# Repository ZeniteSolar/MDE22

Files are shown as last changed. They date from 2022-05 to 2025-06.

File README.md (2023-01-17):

# Electric Steering for Solar Boat

Instituto Federal de Educação, Ciência e Tecnologia de Santa Catarina - Campus Florianópolis

Electronics Academic Department

Degree in Electronics Engineering

Course: Integrative Project III

Professors:

* Robinson Pizzio and Daniel Lohmann

Student:

* Gabriel Ayres Rodrigues

# Summary

1. [Introduction](#introduction)
2. [Conception](#conception)
3. [Design](#design)
4. [Implementation](#implementation)
5. [Operation](#operation)
6. [Considerations](#considerations)
7. [References](#references)

# Introduction

This module aims to control the direction of the tail of the Guarapuvu II vessel, belonging to the IFSC Zênite Solar team.

It is inspired by the previously implemented system, developed by Cesar Dias Parente. The project files can be found [here](https://github.com/ZeniteSolar/MDE18/tree/main).

The Zênite team vessel is operated in solar boat competitions, where high performance and robustness are required. Being the only boat to use electric steering on the competition's context, the team counts on a more reliable system and is able to outmaneuver competition, which is a significant advantage on the Slalom race

The current electronic system was damaged after the competition in March 2022, which is a motivator for its upgrade.

# Conception

Thinking about a steering system, choosing to use an electric steering can bring greater responsiveness even though it has a fraction of the weight of a mechanical system. In addition, mechanical systems can require physical effort from the driver and a greater need for maintenance. 

Below is the diagram representing an electric steering system and its parts.
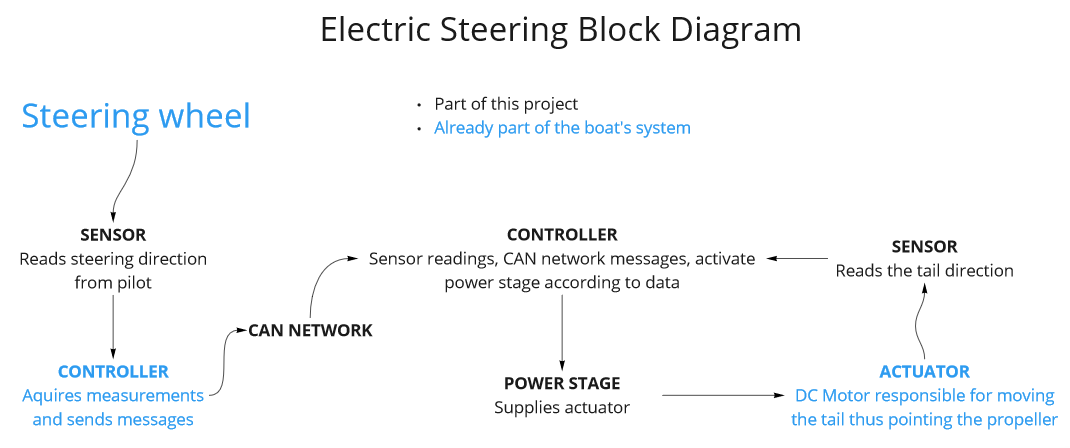
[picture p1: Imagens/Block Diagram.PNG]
Diagram


Taking into account the above elements, the following problems must be confronted:
- Electronic systems in vehicles must have high robustness due to the vibrations to which they are exposed. In the case of high speed vessels, especially for marine operations, impacts are a big problem (besides oxidation of the circuits).
- As the target vehicle is used in competitions whose focus, and therefore the challenge, is on energy generation and consumption, the solution must be as efficient as possible to ensure the success of the team.
- A competitive environment between vehicles requires high performance from this equipment, not only to achieve victory but to ensure everyone's safety. Therefore, the functionality must be met as well as the other parameters.

To implement the whole, it is necessary to define the requirements of the parts, and the possible proposals to satisfy them.

* ## Sensors

There are some options for rotation sensors such as: inductive, optical, Hall effect sensor, rotation potentiometer, encoder. The most economical and simple-to-implement alternative is a common linear potentiometer, currently used in the Zênite team system.

The most used types for steering sensors on the market are the following: resistive, encoders, and those with GMR technology ([Giant magnetoresistance](https://en.wikipedia.org/wiki/Giant_magnetoresistance)). (see the companies considered in [References](#references))

Sensors of this level are state-of-the-art and therefore out of the question, however it is worth noting that the resistive sensor is still being used (even in common vehicles, such as the [butterfly position sensor](https://www.dpk.com.br/como-funciona-o-sensor-de-posicao-da-borboleta/)).

For a contrast between the leaders: resistive sensors have a disadvantage due to wear and possible poor contact, GMR can suffer interference in environments with a strong magnetic field, and encoders (because they are digital) present a challenge in the trade-off Precision X Complexity (thus, price).

Seeking the balance between robustness, ease of implementation and price, the resistive sensor stands out.
 
* ## Controller

The implemented CAN network eliminates the need for cabling with analog signal between the stern and the bow. This ensures noise reduction in sensor readings and takes advantage of existing CAN cabling, compacting the system.

In addition, communication over the network makes it possible for the module to send data and control the direction using messages from other modules. In this way, the range is open for future implementations that may include:

	Redundancy messages and/or sensors
	Low Power Mode - Enabled by the Data Processing Module
	remote steering

A commercial line microcontroller will be enough to guarantee the execution of the desired tasks and response time. In addition to PWM ports and ADC inputs, a microcontroller with a CAN interface like the STM32F103xx or equivalent would be interesting. However, this alternative exceeds the price of IC's transceiver and CAN interface, in addition its programming is more laborious.

Due to its ease of programming and price, the [ATmega328P](https://br.mouser.com/ProductDetail/Microchip-Technology-Atmel/ATMEGA328P-PU?qs=K8BHR703ZXguOQv3sKbWcg%3D%3D) is proposed. For the connection to the CAN network, the most common and affordable IC's are the transceiver
[MCP2551](https://br.mouser.com/datasheet/2/268/20001667G-1115479.pdf) and the CAN/SPI interface circuit [MCP2515](https://br.mouser.com/datasheet/ 2/268/MCP2515_Family_Data_Sheet_DS20001801K-2303489.pdf).

The steering wheel potentiometer reading function will be performed by another module already present in the bow: [MIC19](https://github.com/ZeniteSolar/MIC19)

* ## Power Circuit

The brushed DC motor is driven by an H bridge, currently powered by a 12V battery. The current circuit is implemented by two half-bridge integrated [BTS7960](https://pdf1.alldatasheet.com/datasheet-pdf/view/152657/INFINEON/BTS7960.html).

This component was discontinued, and the best alternative found was [FAN7093](https://www.mouser.com/datasheet/2/149/FAN7093-76982.pdf). As the current one is already in hand and this project is focused on integration and telemetry, the same integrated circuit was used.

* ## Measurements and Feedback

It is essential to provide the CAN network with data on power consumption, as it is a battery-powered power system. Therefore, a current sensor is proposed for each arm of the H-bridge.

Conveniently, the BTS7960 half-bridge integrated circuit has an output pin for current sensing — a current source is connected to the output, and the current IS is proportional to the load current IL according to the measuring resistor RIS.

Alternatively, a circuit like the [INA240](https://www.ti.com/lit/ds/symlink/ina240.pdf?ts=1649772128538) ultra-precise bidirectional current sensor with PWM rejection could be used. From the same family of IC's, the INA826 will be used to measure battery voltage (Hbridge voltage).

These measurements should contribute to the feedback, which will also have the tail position data. Bringing this data to a display ensures that the pilot is aware of the state of the system and the consumption that his riding is causing.

# Design

The module was developed with Kicad software, the project is in the hardware folder of this git and its complete schematic can be viewed [here](https://github.com/ayresgit/Modulo-Direcao-Eletrica/blob/main/hardware/ PDF/steeringmodule.pdf). Below is the general schematic:

General Schematic

The components chosen from the design analysis are the following: Linear Potentiometers, Atmega328P, BTS7960, MCP2515, MCP2551 (or MCP2561), and INA826.

To conform to the vessel's system modules, the following components will also be required:

	2 female RJ45 connectors,
	2 2-way 2EDGRC female terminal (robust and practical, alternative is to use terminal block),
	28-pin stamped socket for the atmega328p,
	zener diodes to protect the microcontroller's ADC,
	2 oscillator crystals

The Kicad software has a function to export a complete list of materials (BOM - Bill Of Materials). It can be found in the hardware folder, at this [link](https://github.com/ZeniteSolar/MDE22/blob/f59e0732b5ff4f93045a860adb85f9820dcc4e83/hardware/steeringmodule.csv).

Right ahead is the PCB 3D preview. As will be explained in the implementation stage, the PCB was made with the help of a milling machine from the institution.

| Front | Back |
| -----  | ----- |
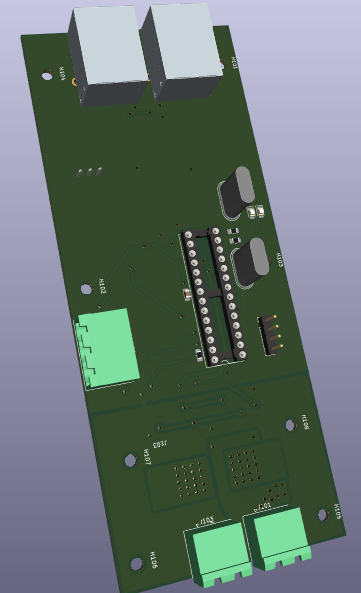
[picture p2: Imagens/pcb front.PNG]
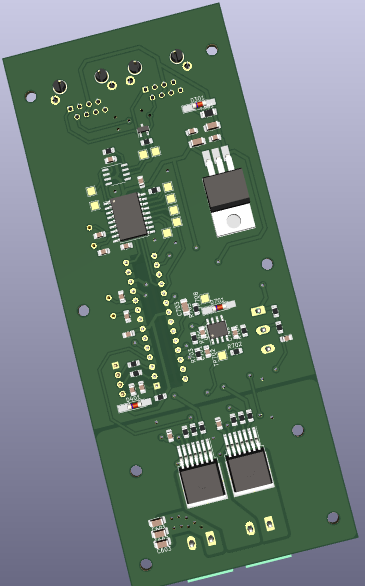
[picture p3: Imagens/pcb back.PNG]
|||

It is worth noting that this repository has an exclusive branch for an ordered board, whose layout was improved and the silkscreen was properly designed to assist in the Implementation stage and possible repairs. This board was not used during the project due to its delivery date.

| Ordered Front | Ordered Back |
| -----  | ----- |
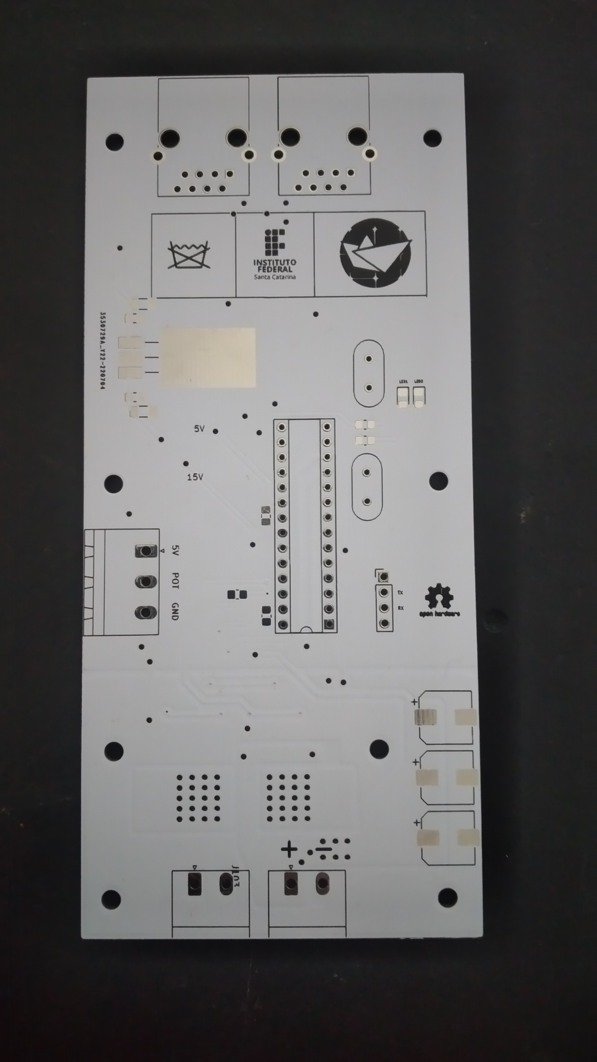
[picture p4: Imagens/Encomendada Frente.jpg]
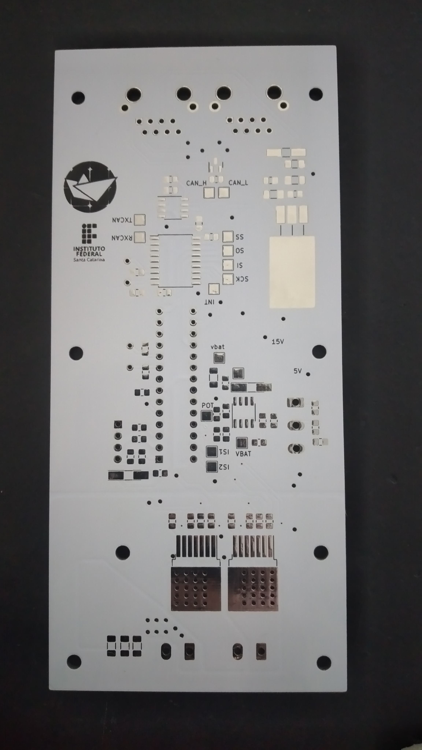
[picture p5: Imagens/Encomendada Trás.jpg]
|||

# Implementation

### PCB manufacturing

The PCB was made by DAELN's CNC milling machine, operated by the department's technicians, the result is shown below. As the manufactured PCB did not have the desired minimum spacing for the power grid, a grinder was used to exclude unwanted tracks — it is important to remember that this type of tool requires the use of PPE.

| Dremel Adjustments | PPE |
| --- | --- |
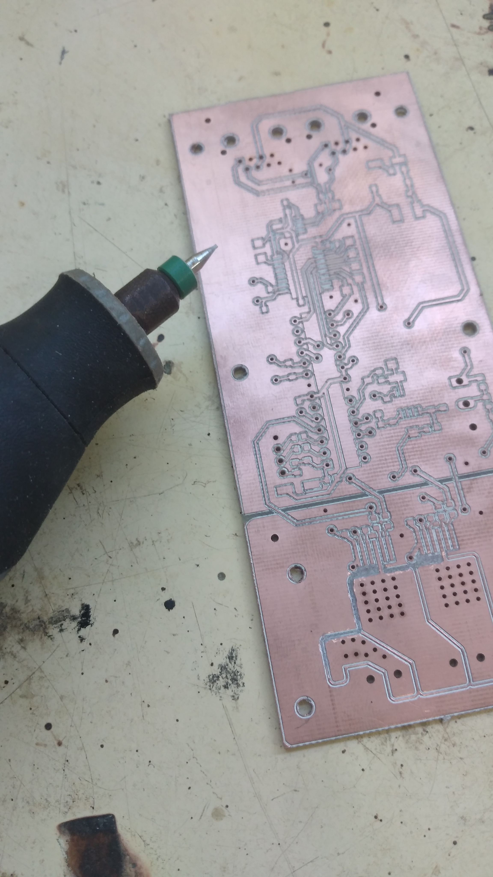
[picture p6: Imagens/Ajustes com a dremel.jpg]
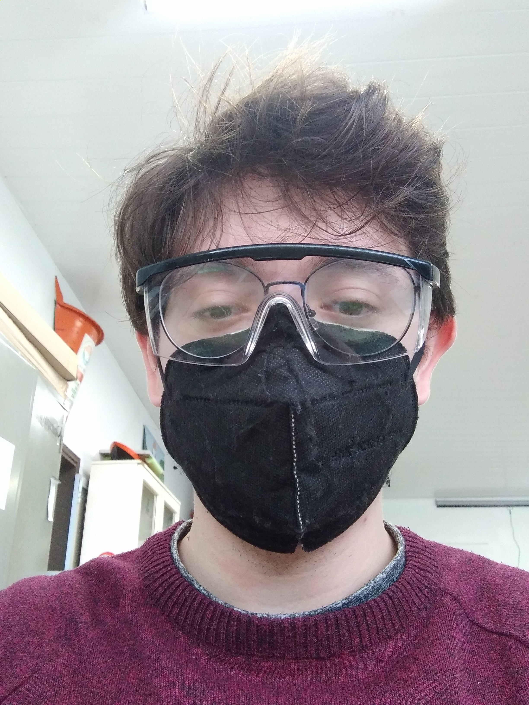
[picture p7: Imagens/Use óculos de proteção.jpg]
||

The board was tinned to protect the circuit against oxidation, and the pathways were made with wires from network cable, cut to size and then soldered in place.

From the order of the components, the soldering was done as follows: SMD, CI, Through-hole connectors being the last ones (to avoid physical stress on the board).

After work on the board, the conclusion was reached that the H-bridge ICs must come before the SMD. This change is interesting because the model needs to be welded with heat, in this case with the aid of a heat gun. The soldered PCB can be seen in the figure.

| Front | Back |
|:-----:|:-----:|
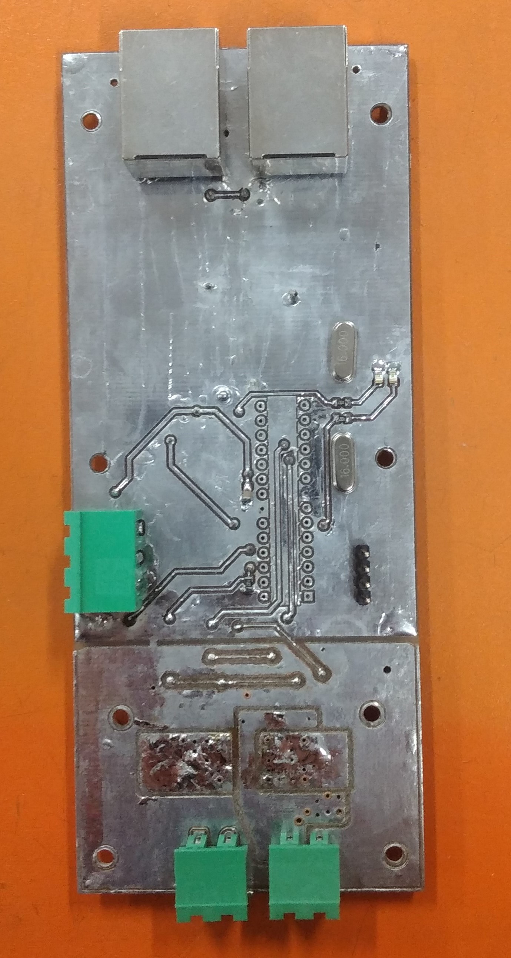
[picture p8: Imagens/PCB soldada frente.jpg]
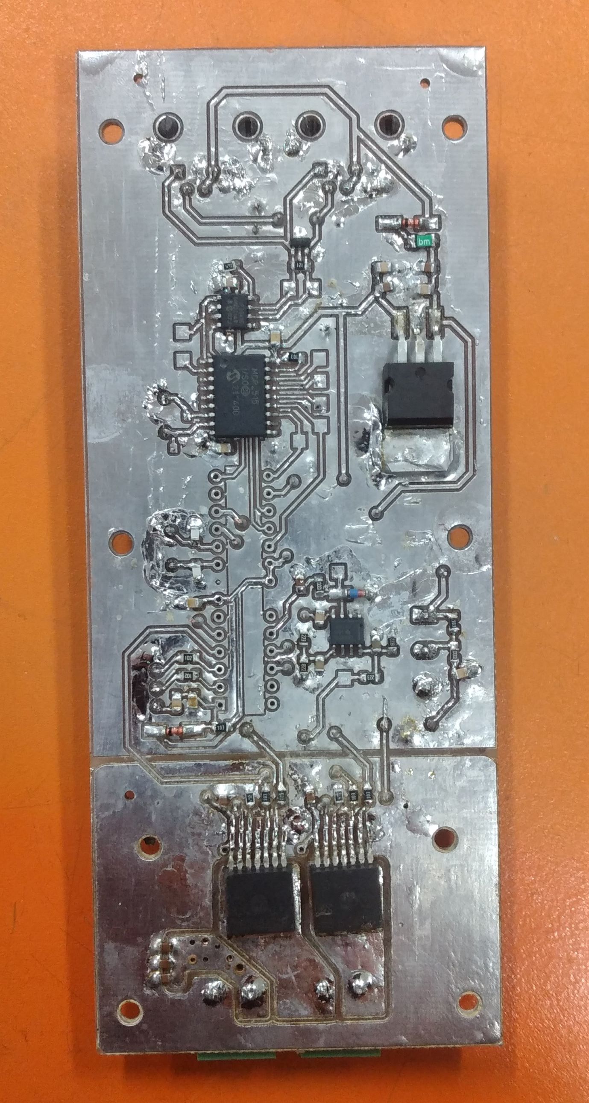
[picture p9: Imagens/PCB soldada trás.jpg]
|||

Once the preparation processes are finished, the microcontroller programming begins, which is done in the C language. The libraries used and the source code can be found in the firmware folder of this repository.

# Operation

The operation stage is divided into two parts: Programming and bench tests. Starting with the basic logic, such as which microcontroller peripherals are used, these steps develop together.

#### Programming

Throughout the process, the microchip datasheet for the atmega328p was used as a reference, which can be found in the [References](#references) of this work.

In the configuration of the peripherals, starting with the ADC, a dilemma was found about the orientation of the system potentiometers. As the system is being upgraded, the current configuration was discarded. It is then defined that the developed code presupposes the following relationships:

| Potentiometer | Tail position |
| --- | --- |
| Maximum value | starboard boundary |
| Average value | centered |
| Minimum value | port limit |

- ADC

The mechanical system that couples the DC motor to the rotation reading potentiometer has a limit close to 270°. The ability to maneuver over 90° to either side has proven useful in the past.
With that in mind, and considering that extreme precision is not required in controlling this angle, the 8-bit ADC is sufficient for all four channels:

- voltage sensor
- current sensor 1 and 2
- Rotation sensor

Each one is configured by the coefficients in adc.c, just operate some measures with unitary coefficients and then do the calculation.

$$ coefficient = {DesiredValue \over ObtainedValue} $$
    
It is interesting to do this test with the full scale value, as the "Desired Value" is naturally known.

- CAN network

Working with the CAN library: the CAN network is implemented from ID's, identifying the modules on the bus and their messages. To generate these IDs, the Zênite team developed a script that generates these values for the module under development.

This path also brings security, ensuring that there will be no equal identities or other conflicts caused by human error and/or parallel development. All of these can be found in the [CAN_IDS](https://github.com/ZeniteSolar/CAN_IDS) repository.

Having the ID's generated for the module and its messages, it is necessary to change the can_filter.h to include the ID's of who you want to listen to (in this case, this project needs to listen to [MIC19](https://github.com/ZeniteSolar/MIC19 )), and create the request and message sending functions in can_app.c/h.

- PWM

Some key points for PWM operation: Chosen timer, prescaler (desired frequency), duty cycle definition (in this case implemented by the set_pwm function in hbridge.c).

Due to an error in the Design stage, the PWM outputs are connected to the ATmega328P's basic timer pins, Timer/Counter 0. The timer's operating mode must be phase correct PWM (which guarantees greater synchronization in relation to Fast PWM). As described in the datasheet, the frequency can be calculated as follows:

$$ fOCnxPWM = {fclkI/O \over {N * 510}} $$

	fOCnxPWM is the PWM frequency on the OCnx ports (in the case of OC0A and OC0B, in PD5 and PD6)
	fclkI/O is the crystal oscillator clock frequency (16MHz)
	N is the configured prescaler

This timer has fewer bits and less functionality compared to the other two. For the application, the only impact was the use of a lower frequency than desired (~3921.5Hz). This happens due to the lack of prescaler options in Timer/Counter0:
    
	prescaler = 1, fPWM = 31.37kHz (exceeds half-bridge IC limits)
	prescaler = 8 --> 3.92kHz (used, suboptimal)

#### Circuit Tests

The bench tests were carried out with the aid of different voltage sources, in the laboratories of the IFSC campus Florianópolis.

<p align="center">
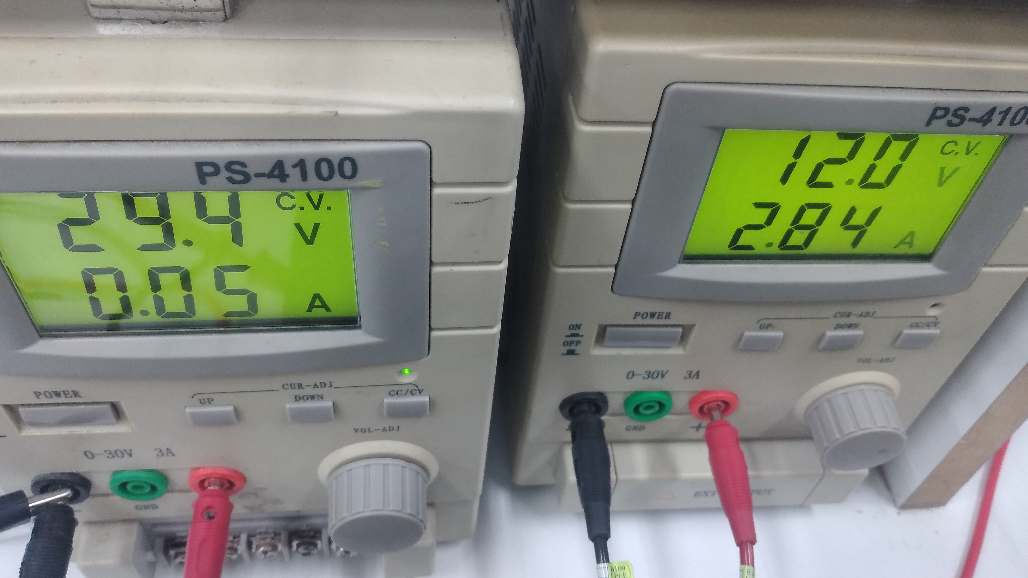
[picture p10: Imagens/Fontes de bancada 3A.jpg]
  

The ADC and CAN network tests were carried out, these results were displayed on the computer by serial communication connecting an arduino to the board's Usart bus.

In the case of PWM, it is necessary to use an oscilloscope, so the figures for some of the tests carried out with the aid of a rheostat are left.

| Duty Cycle 40% Signal | Duty Cycle 40% Values |
| --- | --- |
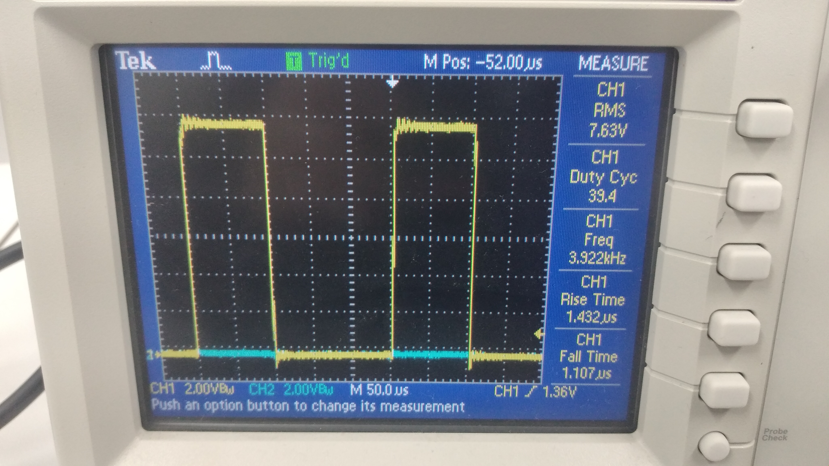
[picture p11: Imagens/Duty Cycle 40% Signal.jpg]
Duty Cycle 40% signal
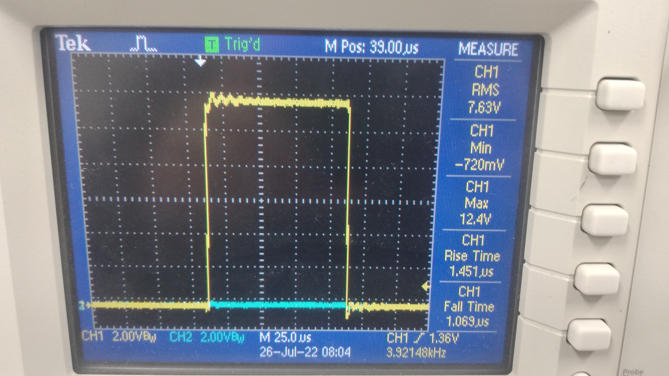
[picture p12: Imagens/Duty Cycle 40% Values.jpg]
Duty Cycle 40% values
|||

| Duty Cycle 80% | Duty Cycle 80% Values |
| --- | --- |
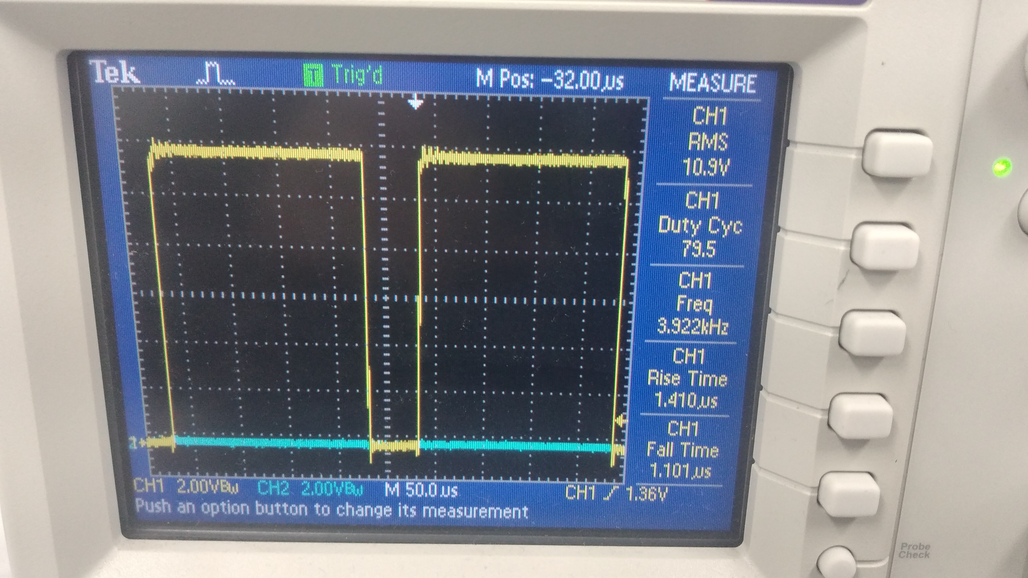
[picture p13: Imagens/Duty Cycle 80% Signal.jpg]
Duty Cycle 80% signal
||Duty Cycle 80% values|

To test the circuit with high current, the resistance in the rheostat was reduced and the duty cycle was maintained:
| Duty Cycle 80% 3A  | Duty Cycle 80% Valores |
| --- | --- |
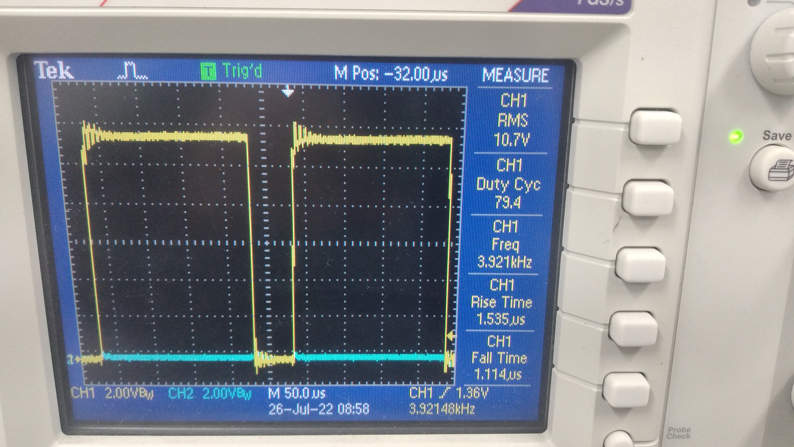
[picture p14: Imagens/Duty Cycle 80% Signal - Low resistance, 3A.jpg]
Duty 80% Signal (3A)
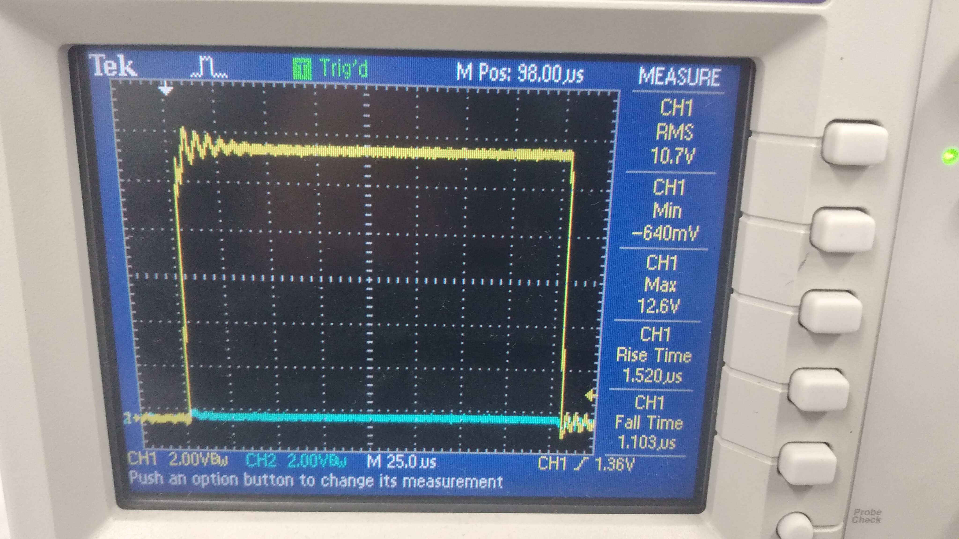
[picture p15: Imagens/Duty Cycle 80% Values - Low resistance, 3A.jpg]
Duty 80% Values (3A)
|||

These results were satisfactory, considering that the circuit was not accumulating heat, the PWM was in accordance with what was desired from the configuration, and the values according to the datasheet.

#### Tests with Engine

The next step is the engine test. Bench test setup is done on the vessel, with bench supplies, boards and necessary connections.

<p align="center">
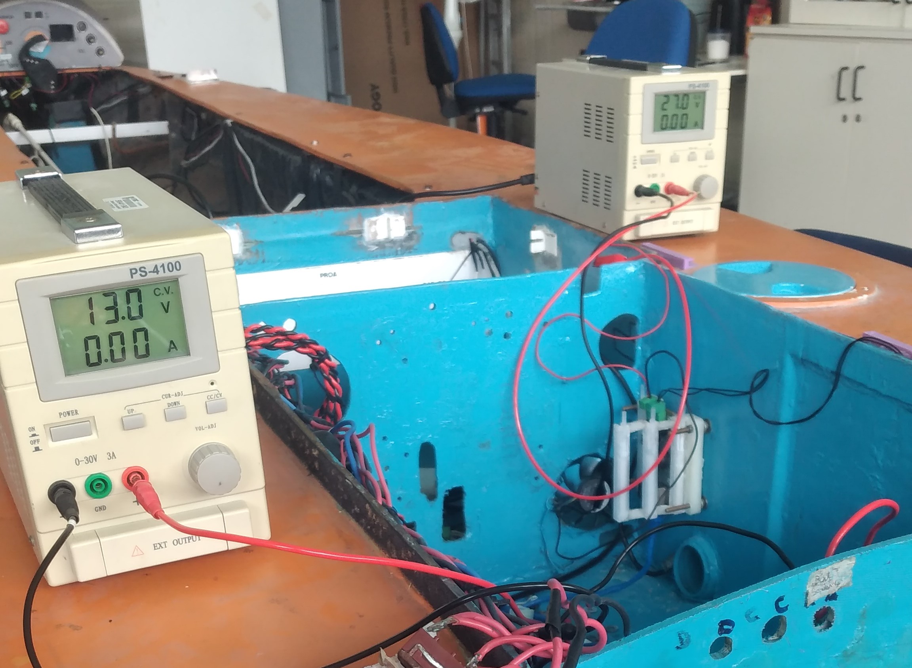
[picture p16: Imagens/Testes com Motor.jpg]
  

During the motor test, operating logics were implemented to the PWM of the H-bridge:

	H bridge activated by the difference between the potentiometers
	centered start
	Forced center if there is no communication
	Reverse side protection

The last logic was considered interesting considering that the system itself is assembled/disassembled for trips to competitions or testing sites.

The mechanical part can be seen in the figure below. The transmission shaft is coupled to the belt by the disc, and the DC steering motor controls the belt.
At the top of this can be seen the potentiometer used to measure rotation.

<p align="center">
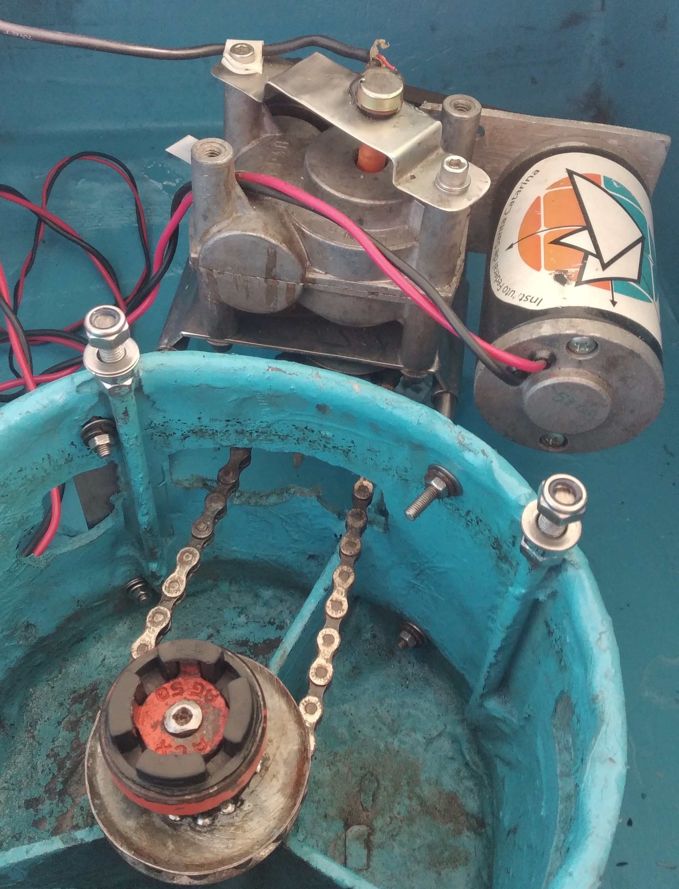
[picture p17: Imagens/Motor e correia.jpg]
  

The engine tests were a success using the bench sources, the operation video is in the Images folder. Due to the file size github cannot run it so it needs to be downloaded. An alternative is to use this [drive link](https://drive.google.com/file/d/12XCSZ1QREOxFkqlZAvMiaMpx_ZMUlxNi/view?usp=sharing).

During the test powered by the 12V battery, the system stopped working. The lack of capacitance for the input voltage caused a failure in one of the half-bridge ICs, after replacing the IC and correcting the values in the schematic the system is safe and operational.

# Considerations

All microcontroller peripherals are functional. All electrical measurements, which were one of the main objectives, showed satisfactory accuracy.

The essential logic of operation is complete, there are safety locks and finally the engine can be controlled smoothly.

Component performance: satisfactory.

Plate manufacturing: poor result, manufacturing caused more work and compromised the robustness of the system. To correctly meet the objective of a more robust system, the PCB ordered must be used.

Below we can see the system assembled with an experimental support — due to the dimensions of the board, a support dedicated to it needs to be manufactured.

On the side, the main power supply module ([MFP19](https://github.com/ZeniteSolar/MFP19)) is shown, which converts the voltage in the battery bank and supplies 18V from the CAN network. Future boat supports are expected to follow this 3D-printed model.

| Assembled System | Support Example |
| --- | --- |
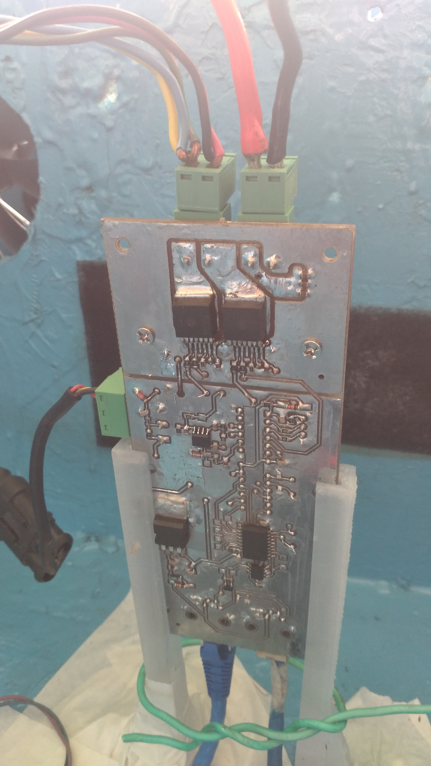
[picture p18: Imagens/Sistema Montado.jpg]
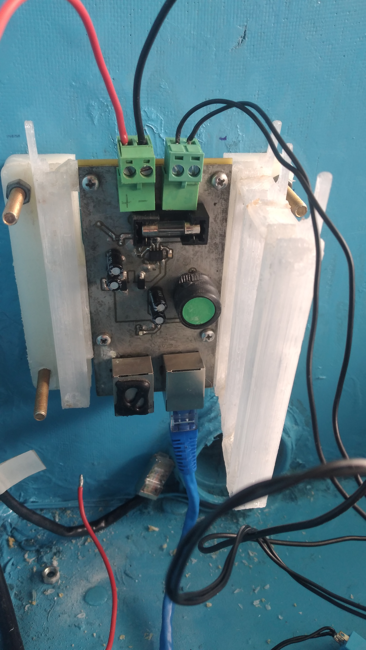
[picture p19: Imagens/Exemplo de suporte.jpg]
|||

For comparison, here are screenshots of the previous system.

| Previous System | H Bridge |
| --- | --- |
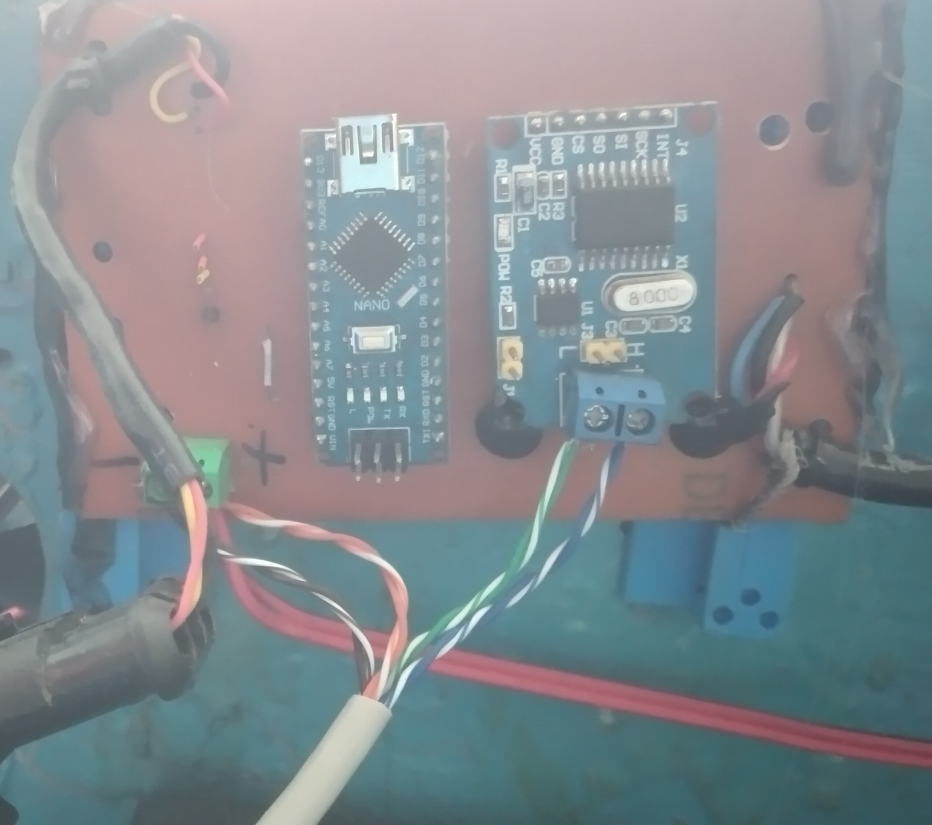
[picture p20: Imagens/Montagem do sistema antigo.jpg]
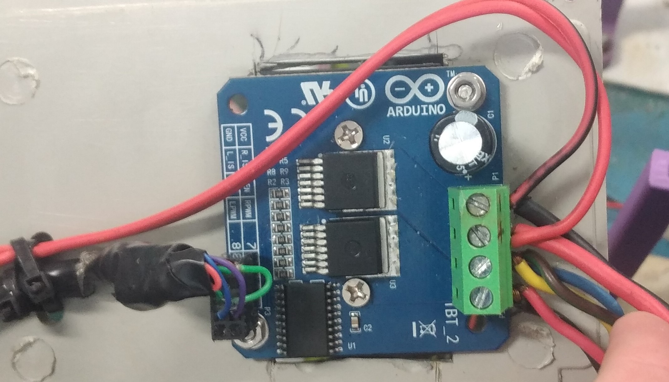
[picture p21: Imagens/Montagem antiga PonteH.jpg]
|||

#### Next steps

Some of the next steps for this module and future updates:

- PWM responsive to pilot movements
- H-Bridge design or choice of non-discontinued IC
- Redundancy messages and/or sensors
- Low power mode - Activated by data processing module
- *Remote steering

*The success of this step would make room for a fascinating update: The Autonomous Boat.

# References

Datasheet ATmega328P:
[Microchip, Atmel ATmega328P](https://ww1.microchip.com/downloads/en/DeviceDoc/Atmel-7810-Automotive-Microcontrollers-ATmega328P_Datasheet.pdf)

Steering sensor market research:
[Bosch](https://www.bosch-motorsport.com/content/downloads/Raceparts/en-GB/120530059.html),
[CUI Inc](https://www.cuidevices.com/catalog/motion/rotary-encoders),
[TT Electronics](https://www.ttelectronics.com/products/categories/steering-sensors/search-results/)

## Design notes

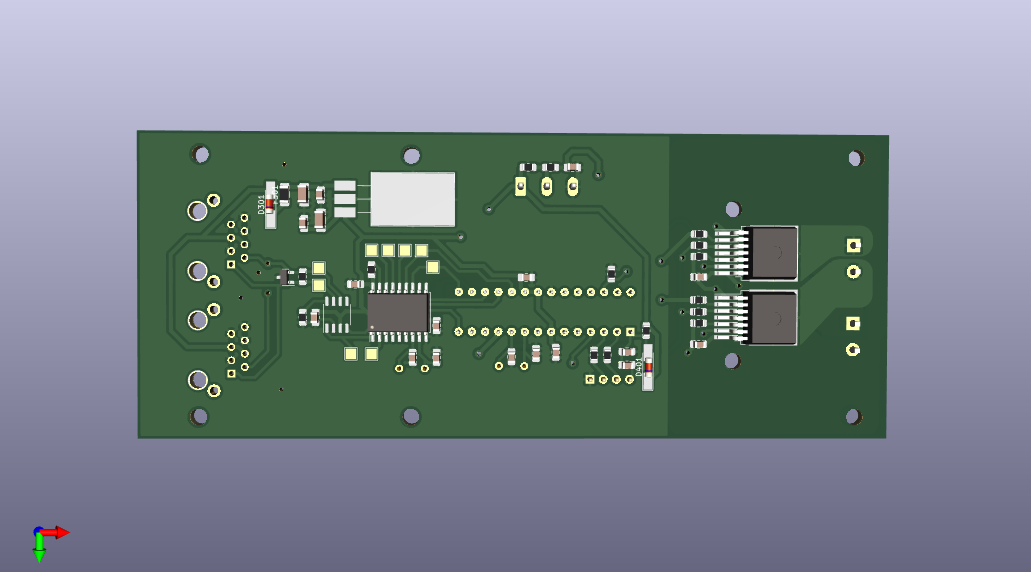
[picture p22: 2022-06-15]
hardware/IMG/steeringmodule_3dback.png

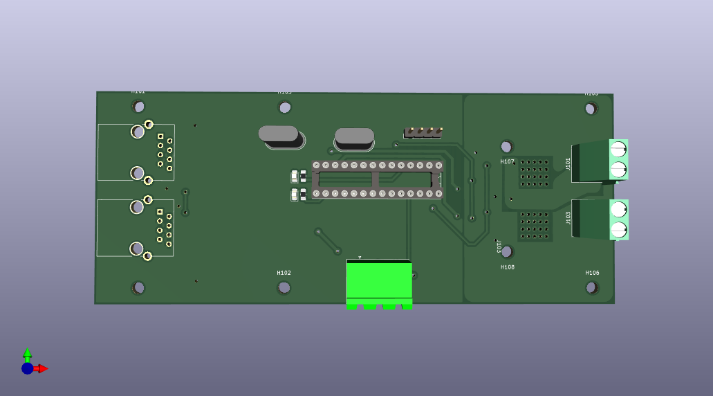
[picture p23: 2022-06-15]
hardware/IMG/steeringmodule_3dfront.png

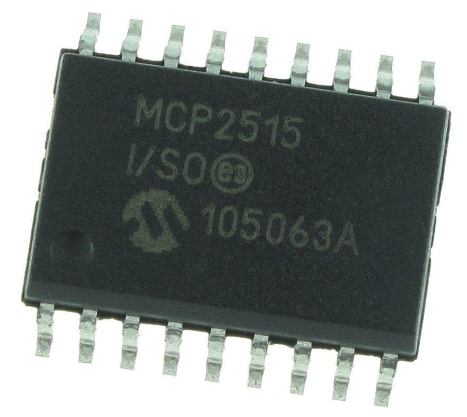
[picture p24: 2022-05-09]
Imagens/MCP2515.PNG

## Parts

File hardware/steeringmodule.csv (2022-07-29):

Source: | C:\Users\gabri\OneDrive\Área de Trabalho\Barco\Módulos Barco\MDE22\hardware\steeringmodule.kicad_sch
Date: | 29/07/2022 06:52:03
Tool: | Eeschema (6.0.4)
Generator: | C:\Program Files\KiCad\6.0\bin\scripting\plugins/bom_csv_grouped_by_value.py
Component Count: | 80
Individual Components:
Item | Qty | Reference(s) | Value | LibPart | Footprint | Datasheet
 |  | C102 | 100nF | Device:C_Small | Capacitor_SMD:C_0805_2012Metric_Pad1.18x1.45mm_HandSolder | ~
 |  | C201 | 100nF | Device:C_Small | Capacitor_SMD:C_0805_2012Metric_Pad1.18x1.45mm_HandSolder | ~
 |  | C202 | 100nF | Device:C_Small | Capacitor_SMD:C_0805_2012Metric_Pad1.18x1.45mm_HandSolder | ~
 |  | C205 | 100nF | Device:C_Small | Capacitor_SMD:C_0805_2012Metric_Pad1.18x1.45mm_HandSolder | ~
 |  | C301 | 1uF | Device:C_Small | Capacitor_SMD:C_1206_3216Metric_Pad1.33x1.80mm_HandSolder | ~
 |  | C302 | 100nF | Device:C_Small | Capacitor_SMD:C_0805_2012Metric_Pad1.18x1.45mm_HandSolder | ~
 |  | C303 | 100nF | Device:C_Small | Capacitor_SMD:C_0805_2012Metric_Pad1.18x1.45mm_HandSolder | ~
 |  | C304 | 1uF | Device:C_Small | Capacitor_SMD:C_1206_3216Metric_Pad1.33x1.80mm_HandSolder | ~
 |  | C401 | 100nF | Device:C_Small | Capacitor_SMD:C_0805_2012Metric_Pad1.18x1.45mm_HandSolder | ~
 |  | C402 | 100nF | Device:C_Small | Capacitor_SMD:C_0805_2012Metric_Pad1.18x1.45mm_HandSolder | ~
 |  | C403 | 22pF | Device:C_Small | Capacitor_SMD:C_0805_2012Metric_Pad1.18x1.45mm_HandSolder | ~
 |  | C404 | 22pF | Device:C_Small | Capacitor_SMD:C_0805_2012Metric_Pad1.18x1.45mm_HandSolder | ~
 |  | C405 | 100nF | Device:C_Small | Capacitor_SMD:C_0805_2012Metric_Pad1.18x1.45mm_HandSolder | ~
 |  | C406 | 100nF | Device:C_Small | Capacitor_SMD:C_0805_2012Metric_Pad1.18x1.45mm_HandSolder | ~
 |  | C407 | 22pF | Device:C_Small | Capacitor_SMD:C_0805_2012Metric_Pad1.18x1.45mm_HandSolder | ~
 |  | C408 | 22pF | Device:C_Small | Capacitor_SMD:C_0805_2012Metric_Pad1.18x1.45mm_HandSolder | ~
 |  | C601 | 1uF | Device:C_Small | Capacitor_SMD:C_1206_3216Metric_Pad1.33x1.80mm_HandSolder | ~
 |  | C602 | 1uF | Device:C_Small | Capacitor_SMD:C_1206_3216Metric_Pad1.33x1.80mm_HandSolder | ~
 |  | C603 | 1uF | Device:C_Small | Capacitor_SMD:C_1206_3216Metric_Pad1.33x1.80mm_HandSolder | ~
 |  | C701 | 1n | Device:C_Small | Capacitor_SMD:C_0805_2012Metric_Pad1.18x1.45mm_HandSolder | ~
 |  | C702 | 1n | Device:C_Small | Capacitor_SMD:C_0805_2012Metric_Pad1.18x1.45mm_HandSolder | ~
 |  | C703 | 1uF | Device:C_Small | Capacitor_SMD:C_1206_3216Metric_Pad1.33x1.80mm_HandSolder | ~
 |  | C704 | 100n | Device:C_Small | Capacitor_SMD:C_0805_2012Metric_Pad1.18x1.45mm_HandSolder | ~
 |  | CBTS1 | 470nF | Device:C_Small | Capacitor_SMD:C_0805_2012Metric_Pad1.18x1.45mm_HandSolder | ~
 |  | CBTS2 | 470nF | Device:C_Small | Capacitor_SMD:C_0805_2012Metric_Pad1.18x1.45mm_HandSolder | ~
 |  | D301 | LL4148 | Diode:LL4148 | Diode_SMD:D_MiniMELF | http://www.vishay.com/docs/85557/ll4148.pdf
 |  | D401 | LL4148 | Diode:LL4148 | Diode_SMD:D_MiniMELF | http://www.vishay.com/docs/85557/ll4148.pdf
 |  | D402 | LED_RED | Device:LED_Small | LED_SMD:LED_0805_2012Metric_Pad1.15x1.40mm_HandSolder | ~
 |  | D403 | LED_GRN | Device:LED_Small | LED_SMD:LED_0805_2012Metric_Pad1.15x1.40mm_HandSolder | ~
 |  | D404 | D_TVS_Dual_AAC | Device:D_TVS_Dual_AAC | Package_TO_SOT_SMD:SOT-23 | ~
 |  | D701 | 4V7 | Device:D_Zener_Small | Diode_SMD:D_MiniMELF_Handsoldering | ~
 |  | F301 | Fuse | Device:Fuse | Fuse:Fuse_1206_3216Metric_Pad1.42x1.75mm_HandSolder | ~
 |  | H101 | MountingHole | Mechanical:MountingHole | MountingHole:MountingHole_3.2mm_M3 | ~
 |  | H102 | MountingHole | Mechanical:MountingHole | MountingHole:MountingHole_3.2mm_M3 | ~
 |  | H103 | MountingHole | Mechanical:MountingHole | MountingHole:MountingHole_3.2mm_M3 | ~
 |  | H104 | MountingHole | Mechanical:MountingHole | MountingHole:MountingHole_3.2mm_M3 | ~
 |  | H105 | MountingHole | Mechanical:MountingHole | MountingHole:MountingHole_3.2mm_M3 | ~
 |  | H106 | MountingHole | Mechanical:MountingHole | MountingHole:MountingHole_3.2mm_M3 | ~
 |  | H107 | MountingHole | Mechanical:MountingHole | MountingHole:MountingHole_3.2mm_M3 | ~
 |  | H108 | MountingHole | Mechanical:MountingHole | MountingHole:MountingHole_3.2mm_M3 | ~
 |  | J101 | Conn_01x02 | Connector_Generic:Conn_01x02 | Connector_Phoenix_MSTB:PhoenixContact_MSTBA_2,5_2-G-5,08_1x02_P5.08mm_Horizontal | ~
 |  | J102 | PotConnector | Connector_Generic:Conn_01x03 | Connector_Phoenix_MSTB:PhoenixContact_MSTBA_2,5_3-G-5,08_1x03_P5.08mm_Horizontal | ~
 |  | J103 | Conn_01x02 | Connector_Generic:Conn_01x02 | Connector_Phoenix_MSTB:PhoenixContact_MSTBA_2,5_2-G-5,08_1x02_P5.08mm_Horizontal | ~
 |  | J201 | ~ | :RJ45_Shielded_1 | KicadZeniteSolarLibrary18:RJ45_YH59_01
 |  | J202 | ~ | Connector:RJ45_Shielded | KicadZeniteSolarLibrary18:RJ45_YH59_01
 |  | J401 | ~ | Connector_Generic:Conn_01x04 | Connector_PinHeader_2.54mm:PinHeader_1x04_P2.54mm_Vertical | ~
 |  | R101 | 100 | Device:R_Small | Resistor_SMD:R_0805_2012Metric_Pad1.20x1.40mm_HandSolder | ~
 |  | R102 | 10k | Device:R_Small | Resistor_SMD:R_0805_2012Metric_Pad1.20x1.40mm_HandSolder | ~
 |  | R201 | 120 | Device:R_Small | Resistor_SMD:R_0805_2012Metric_Pad1.20x1.40mm_HandSolder | ~
 |  | R202 | 4k7 | Device:R_Small | Resistor_SMD:R_0805_2012Metric_Pad1.20x1.40mm_HandSolder | ~
 |  | R203 | 10k | Device:R_Small | Resistor_SMD:R_0805_2012Metric_Pad1.20x1.40mm_HandSolder | ~
 |  | R401 | 10k | Device:R_Small | Resistor_SMD:R_0805_2012Metric_Pad1.20x1.40mm_HandSolder | ~
 |  | R402 | 1k | Device:R_Small | Resistor_SMD:R_0805_2012Metric_Pad1.20x1.40mm_HandSolder | ~
 |  | R403 | 1k | Device:R_Small | Resistor_SMD:R_0805_2012Metric_Pad1.20x1.40mm_HandSolder | ~
 |  | R404 | 1k | Device:R_Small | Resistor_SMD:R_0805_2012Metric_Pad1.20x1.40mm_HandSolder | ~
 |  | R405 | 1k | Device:R_Small | Resistor_SMD:R_0805_2012Metric_Pad1.20x1.40mm_HandSolder | ~
 |  | R701 | 22k | Device:R_Small | Resistor_SMD:R_0805_2012Metric_Pad1.20x1.40mm_HandSolder | ~
 |  | R702 | 22k | Device:R_Small | Resistor_SMD:R_0805_2012Metric_Pad1.20x1.40mm_HandSolder | ~
 |  | R703 | 8k2 | Device:R_Small | Resistor_SMD:R_0805_2012Metric_Pad1.20x1.40mm_HandSolder | ~
 |  | R704 | 8k2 | Device:R_Small | Resistor_SMD:R_0805_2012Metric_Pad1.20x1.40mm_HandSolder | ~
 |  | R705 | 100 | Device:R_Small | Resistor_SMD:R_0805_2012Metric_Pad1.20x1.40mm_HandSolder | ~
 |  | RINH1 | 10k | Device:R_Small | Resistor_SMD:R_0805_2012Metric_Pad1.20x1.40mm_HandSolder | ~
 |  | RINH2 | 10k | Device:R_Small | Resistor_SMD:R_0805_2012Metric_Pad1.20x1.40mm_HandSolder | ~
 |  | RIS1 | 1k | Device:R_Small | Resistor_SMD:R_0805_2012Metric_Pad1.20x1.40mm_HandSolder | ~
 |  | RSR1 | 5k1 | Device:R_Small | Resistor_SMD:R_0805_2012Metric_Pad1.20x1.40mm_HandSolder | ~
 |  | RSR2 | 5k1 | Device:R_Small | Resistor_SMD:R_0805_2012Metric_Pad1.20x1.40mm_HandSolder | ~
 |  | RSR601 | 10k | Device:R_Small | Resistor_SMD:R_0805_2012Metric_Pad1.20x1.40mm_HandSolder | ~
 |  | RSR603 | 10k | Device:R_Small | Resistor_SMD:R_0805_2012Metric_Pad1.20x1.40mm_HandSolder | ~
 |  | TP405 | TestPoint | Connector:TestPoint | TestPoint:TestPoint_Pad_2.0x2.0mm | ~
 |  | TP702 | VBAT | Connector:TestPoint | TestPoint:TestPoint_Pad_2.0x2.0mm | ~
 |  | TP708 | out1 | Connector:TestPoint | TestPoint:TestPoint_Pad_2.0x2.0mm | ~
 |  | U201 | MCP2561-E/SN | Interface_CAN_LIN:MCP2561-E-SN | Package_SO:SO-8_3.9x4.9mm_P1.27mm | http://ww1.microchip.com/downloads/en/DeviceDoc/25167A.pdf
 |  | U202 | MCP2515-I/SO | basicsensormodule-rescue:MCP2515-xSO-Interface_CAN_LIN | Package_SO:SOIC-18W_7.5x11.6mm_P1.27mm | http://ww1.microchip.com/downloads/en/DeviceDoc/21801e.pdf
 |  | U301 | LM7805_TO220 | Regulator_Linear:LM7805_TO220 | KicadZeniteSolarLibrary18:TO-220-3_Horizontal_TabDown_SMD | https://www.onsemi.cn/PowerSolutions/document/MC7800-D.PDF
 |  | U401 | ATMEGA328P-PU | basicsensormodule-rescue:ATmega328P-PU-MCU_Microchip_ATmega | Package_DIP:DIP-28_W7.62mm_Socket
 |  | U601 | BTS7960B | BTS7960B:BTS7960B | Package_TO_SOT_SMD:TO-263-7_TabPin8
 |  | U602 | BTS7960B | BTS7960B:BTS7960B | Package_TO_SOT_SMD:TO-263-7_TabPin8
 |  | U701 | INA826_D_8 | INA826AIDR:INA826_D_8 | Package_SO:SOIC-8_3.9x4.9mm_P1.27mm
 |  | Y401 | 16MHz | Device:Crystal_Small | Crystal:Crystal_HC49-U_Vertical | http://www.farnell.com/datasheets/321153.pdf
 |  | Y402 | 16MHz | Device:Crystal_Small | Crystal:Crystal_HC49-U_Vertical | http://www.farnell.com/datasheets/321153.pdf
Collated Components:
Item | Qty | Reference(s) | Value | LibPart | Footprint | Datasheet
1 | 10 | C102, C201, C202, C205, C302, C303, C401, C402, C405, C406 | 100nF | Device:C_Small | Capacitor_SMD:C_0805_2012Metric_Pad1.18x1.45mm_HandSolder | ~
2 | 6 | C301, C304, C601, C602, C603, C703 | 1uF | Device:C_Small | Capacitor_SMD:C_1206_3216Metric_Pad1.33x1.80mm_HandSolder | ~
3 | 4 | C403, C404, C407, C408 | 22pF | Device:C_Small | Capacitor_SMD:C_0805_2012Metric_Pad1.18x1.45mm_HandSolder | ~
4 | 2 | C701, C702 | 1n | Device:C_Small | Capacitor_SMD:C_0805_2012Metric_Pad1.18x1.45mm_HandSolder | ~
5 | 1 | C704 | 100n | Device:C_Small | Capacitor_SMD:C_0805_2012Metric_Pad1.18x1.45mm_HandSolder | ~
6 | 2 | CBTS1, CBTS2 | 470nF | Device:C_Small | Capacitor_SMD:C_0805_2012Metric_Pad1.18x1.45mm_HandSolder | ~
7 | 2 | D301, D401 | LL4148 | Diode:LL4148 | Diode_SMD:D_MiniMELF | http://www.vishay.com/docs/85557/ll4148.pdf
8 | 1 | D402 | LED_RED | Device:LED_Small | LED_SMD:LED_0805_2012Metric_Pad1.15x1.40mm_HandSolder | ~
9 | 1 | D403 | LED_GRN | Device:LED_Small | LED_SMD:LED_0805_2012Metric_Pad1.15x1.40mm_HandSolder | ~
10 | 1 | D404 | D_TVS_Dual_AAC | Device:D_TVS_Dual_AAC | Package_TO_SOT_SMD:SOT-23 | ~
11 | 1 | D701 | 4V7 | Device:D_Zener_Small | Diode_SMD:D_MiniMELF_Handsoldering | ~
12 | 1 | F301 | Fuse | Device:Fuse | Fuse:Fuse_1206_3216Metric_Pad1.42x1.75mm_HandSolder | ~
13 | 8 | H101, H102, H103, H104, H105, H106, H107, H108 | MountingHole | Mechanical:MountingHole | MountingHole:MountingHole_3.2mm_M3 | ~
14 | 2 | J101, J103 | Conn_01x02 | Connector_Generic:Conn_01x02 | Connector_Phoenix_MSTB:PhoenixContact_MSTBA_2,5_2-G-5,08_1x02_P5.08mm_Horizontal | ~
15 | 1 | J102 | PotConnector | Connector_Generic:Conn_01x03 | Connector_Phoenix_MSTB:PhoenixContact_MSTBA_2,5_3-G-5,08_1x03_P5.08mm_Horizontal | ~
16 | 1 | J201 | ~ | :RJ45_Shielded_1 | KicadZeniteSolarLibrary18:RJ45_YH59_01
17 | 1 | J202 | ~ | Connector:RJ45_Shielded | KicadZeniteSolarLibrary18:RJ45_YH59_01
18 | 1 | J401 | ~ | Connector_Generic:Conn_01x04 | Connector_PinHeader_2.54mm:PinHeader_1x04_P2.54mm_Vertical | ~
19 | 2 | R101, R705 | 100 | Device:R_Small | Resistor_SMD:R_0805_2012Metric_Pad1.20x1.40mm_HandSolder | ~
20 | 7 | R102, R203, R401, RINH1, RINH2, RSR601, RSR603 | 10k | Device:R_Small | Resistor_SMD:R_0805_2012Metric_Pad1.20x1.40mm_HandSolder | ~
21 | 1 | R201 | 120 | Device:R_Small | Resistor_SMD:R_0805_2012Metric_Pad1.20x1.40mm_HandSolder | ~
22 | 1 | R202 | 4k7 | Device:R_Small | Resistor_SMD:R_0805_2012Metric_Pad1.20x1.40mm_HandSolder | ~
23 | 5 | R402, R403, R404, R405, RIS1 | 1k | Device:R_Small | Resistor_SMD:R_0805_2012Metric_Pad1.20x1.40mm_HandSolder | ~
24 | 2 | R701, R702 | 22k | Device:R_Small | Resistor_SMD:R_0805_2012Metric_Pad1.20x1.40mm_HandSolder | ~
25 | 2 | R703, R704 | 8k2 | Device:R_Small | Resistor_SMD:R_0805_2012Metric_Pad1.20x1.40mm_HandSolder | ~
26 | 2 | RSR1, RSR2 | 5k1 | Device:R_Small | Resistor_SMD:R_0805_2012Metric_Pad1.20x1.40mm_HandSolder | ~
27 | 1 | TP405 | TestPoint | Connector:TestPoint | TestPoint:TestPoint_Pad_2.0x2.0mm | ~
28 | 1 | TP702 | VBAT | Connector:TestPoint | TestPoint:TestPoint_Pad_2.0x2.0mm | ~
29 | 1 | TP708 | out1 | Connector:TestPoint | TestPoint:TestPoint_Pad_2.0x2.0mm | ~
30 | 1 | U201 | MCP2561-E/SN | Interface_CAN_LIN:MCP2561-E-SN | Package_SO:SO-8_3.9x4.9mm_P1.27mm | http://ww1.microchip.com/downloads/en/DeviceDoc/25167A.pdf
31 | 1 | U202 | MCP2515-I/SO | basicsensormodule-rescue:MCP2515-xSO-Interface_CAN_LIN | Package_SO:SOIC-18W_7.5x11.6mm_P1.27mm | http://ww1.microchip.com/downloads/en/DeviceDoc/21801e.pdf
32 | 1 | U301 | LM7805_TO220 | Regulator_Linear:LM7805_TO220 | KicadZeniteSolarLibrary18:TO-220-3_Horizontal_TabDown_SMD | https://www.onsemi.cn/PowerSolutions/document/MC7800-D.PDF
33 | 1 | U401 | ATMEGA328P-PU | basicsensormodule-rescue:ATmega328P-PU-MCU_Microchip_ATmega | Package_DIP:DIP-28_W7.62mm_Socket
34 | 2 | U601, U602 | BTS7960B | BTS7960B:BTS7960B | Package_TO_SOT_SMD:TO-263-7_TabPin8
35 | 1 | U701 | INA826_D_8 | INA826AIDR:INA826_D_8 | Package_SO:SOIC-8_3.9x4.9mm_P1.27mm
36 | 2 | Y401, Y402 | 16MHz | Device:Crystal_Small | Crystal:Crystal_HC49-U_Vertical | http://www.farnell.com/datasheets/321153.pdf

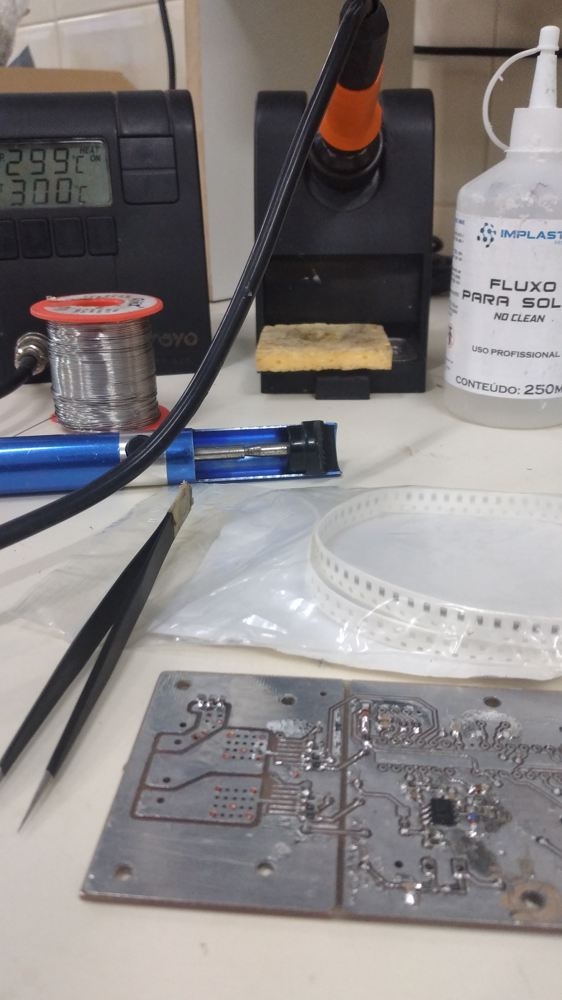
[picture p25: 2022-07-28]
Imagens/Soldagem dos componentes.jpg

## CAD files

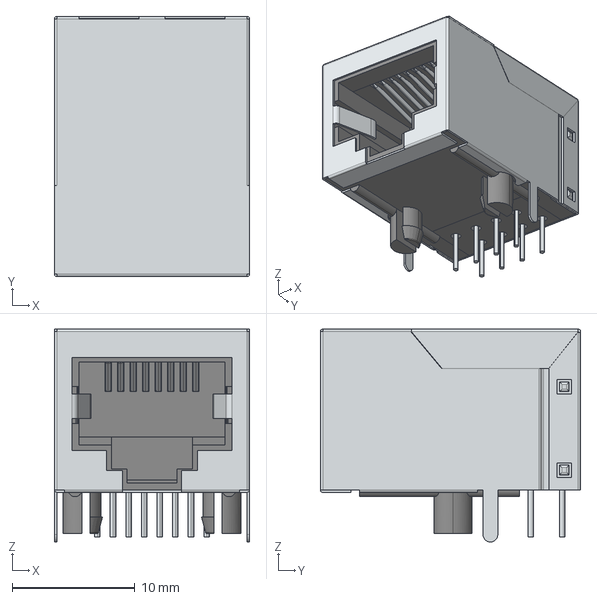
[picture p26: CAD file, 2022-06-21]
hardware/Bibliotecas/rj45.step
15.9 x 21.2 x 17.3 mm

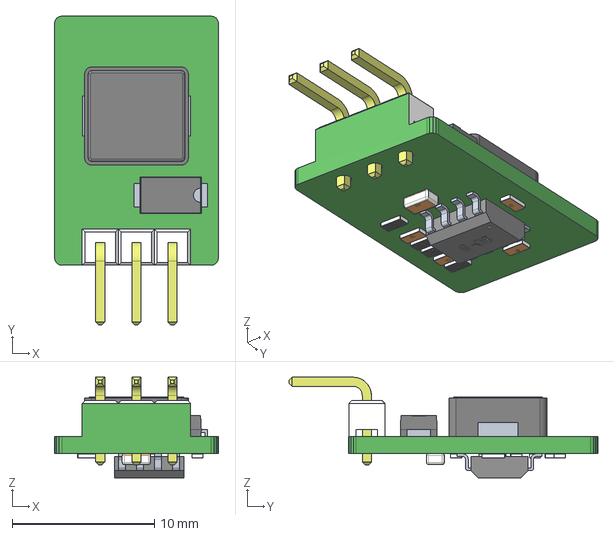
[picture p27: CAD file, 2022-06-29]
hardware/shapes3D/K78Lxx-1000R3.stp
11.5 x 21.7 x 7.08 mm

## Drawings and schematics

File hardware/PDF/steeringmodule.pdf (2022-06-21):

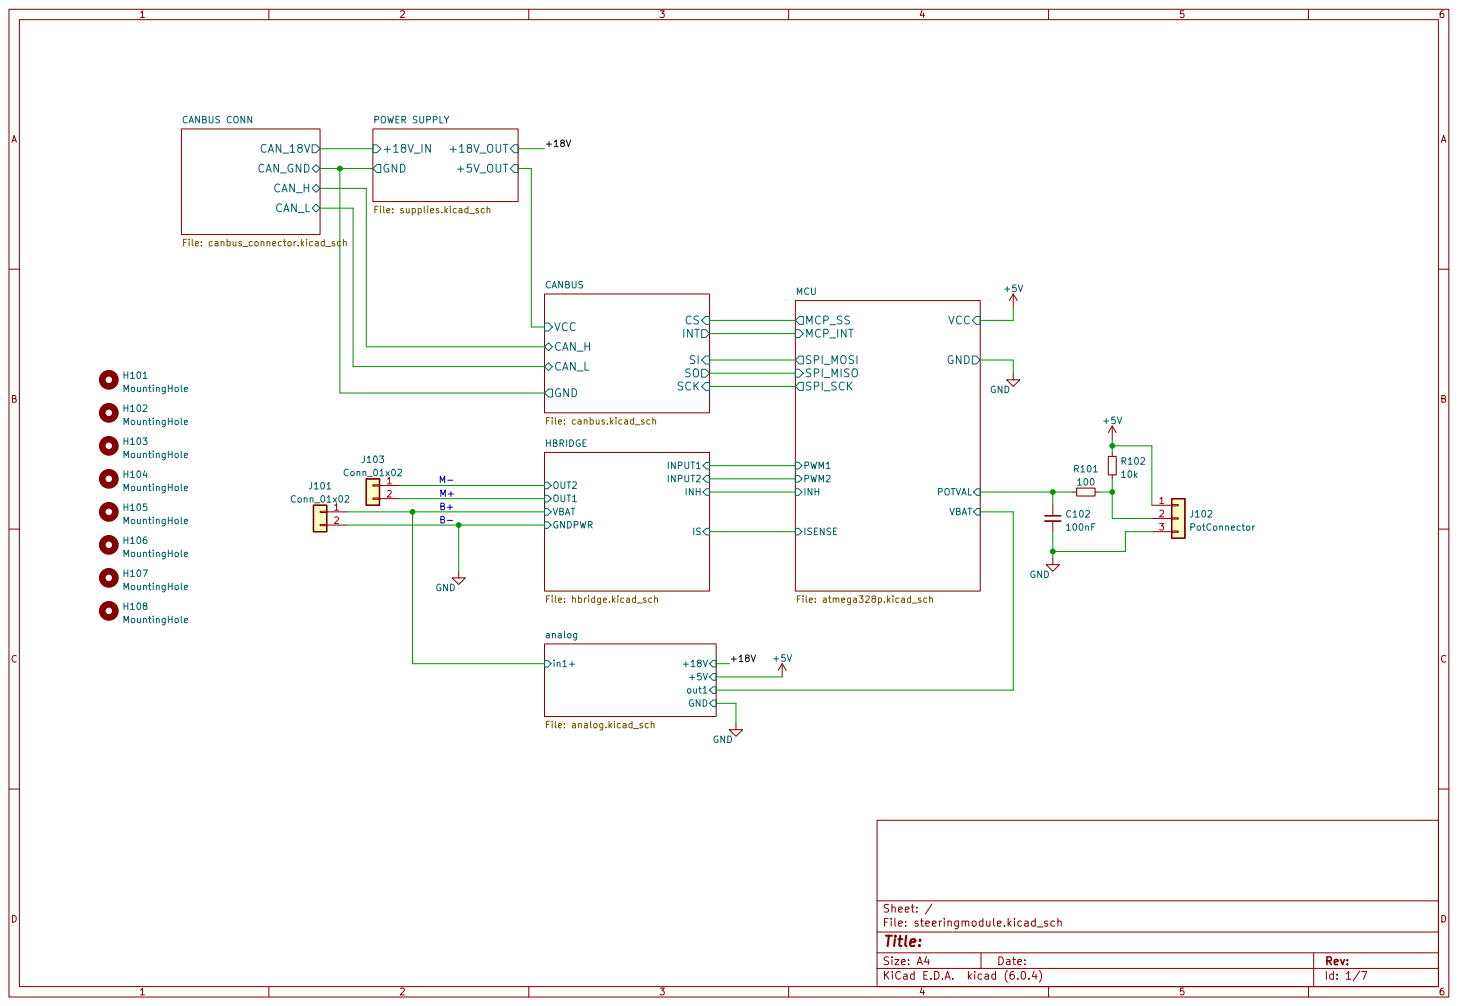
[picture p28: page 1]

J101 Conn_01x02 H107 MountingHole H108 MountingHole H102 MountingHole H104 MountingHole H105 MountingHole

File: steeringmodule.kicad_sch Sheet: / OUT2 OUT1 GNDPWR

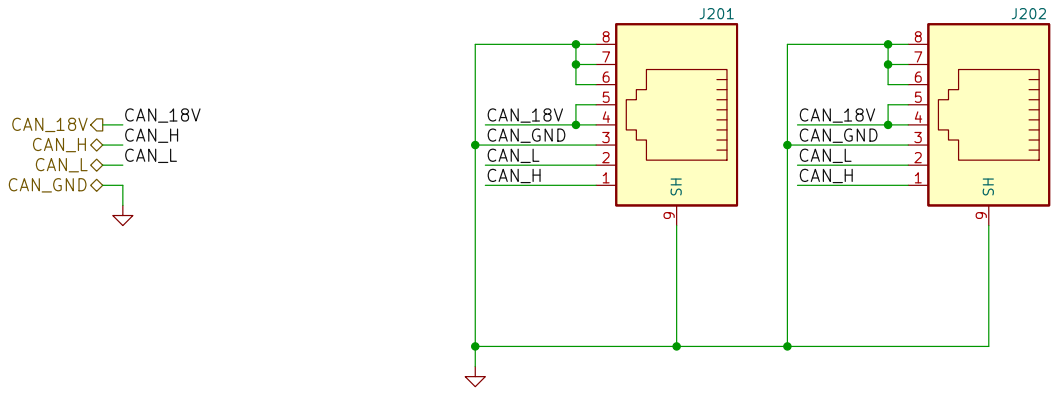
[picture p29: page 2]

File: canbus_connector.kicad_sch Sheet: /CANBUS CONN/
Id: 2/7 Title:

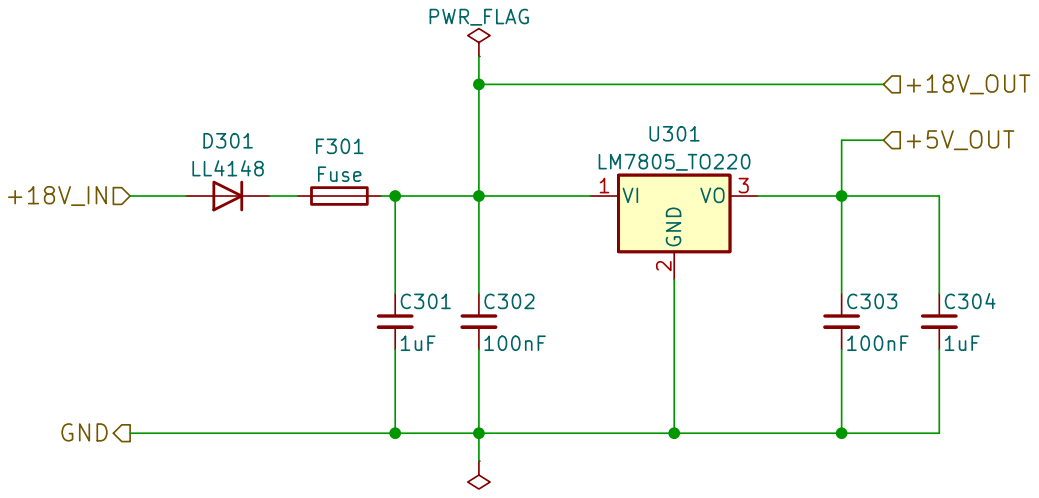
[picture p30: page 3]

File: supplies.kicad_sch Sheet: /POWER SUPPLY/ D301

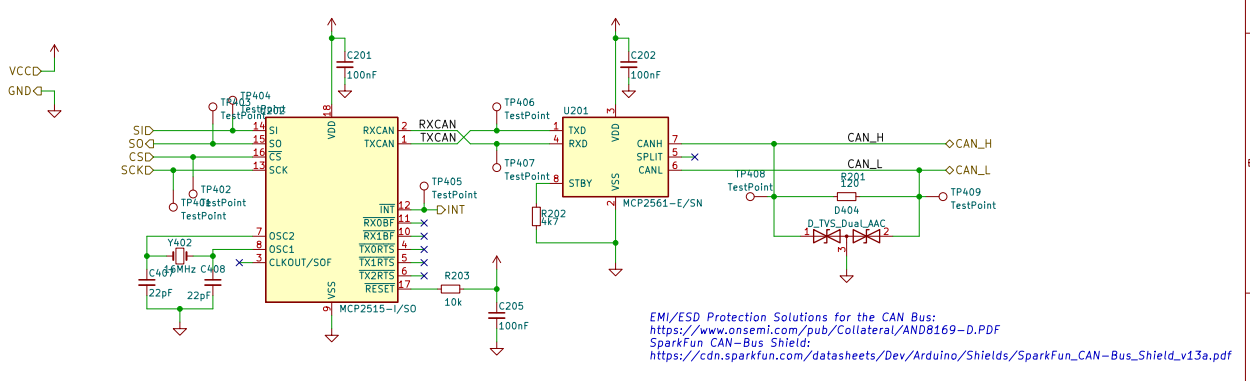
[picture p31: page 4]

3 RXD 4 SPLIT 5 CANL 6 CANH 7 STBY 8 U201 MCP2561-E/SN

EMI/ESD Protection Solutions for the CAN Bus:
https://www.onsemi.com/pub/Collateral/AND8169-D.PDF
SparkFun CAN-Bus Shield:
https://cdn.sparkfun.com/datasheets/Dev/Arduino/Shields/SparkFun_CAN-Bus_Shield_v13a.pdf

File: canbus.kicad_sch Sheet: /CANBUS/
Id: 4/7 Title:

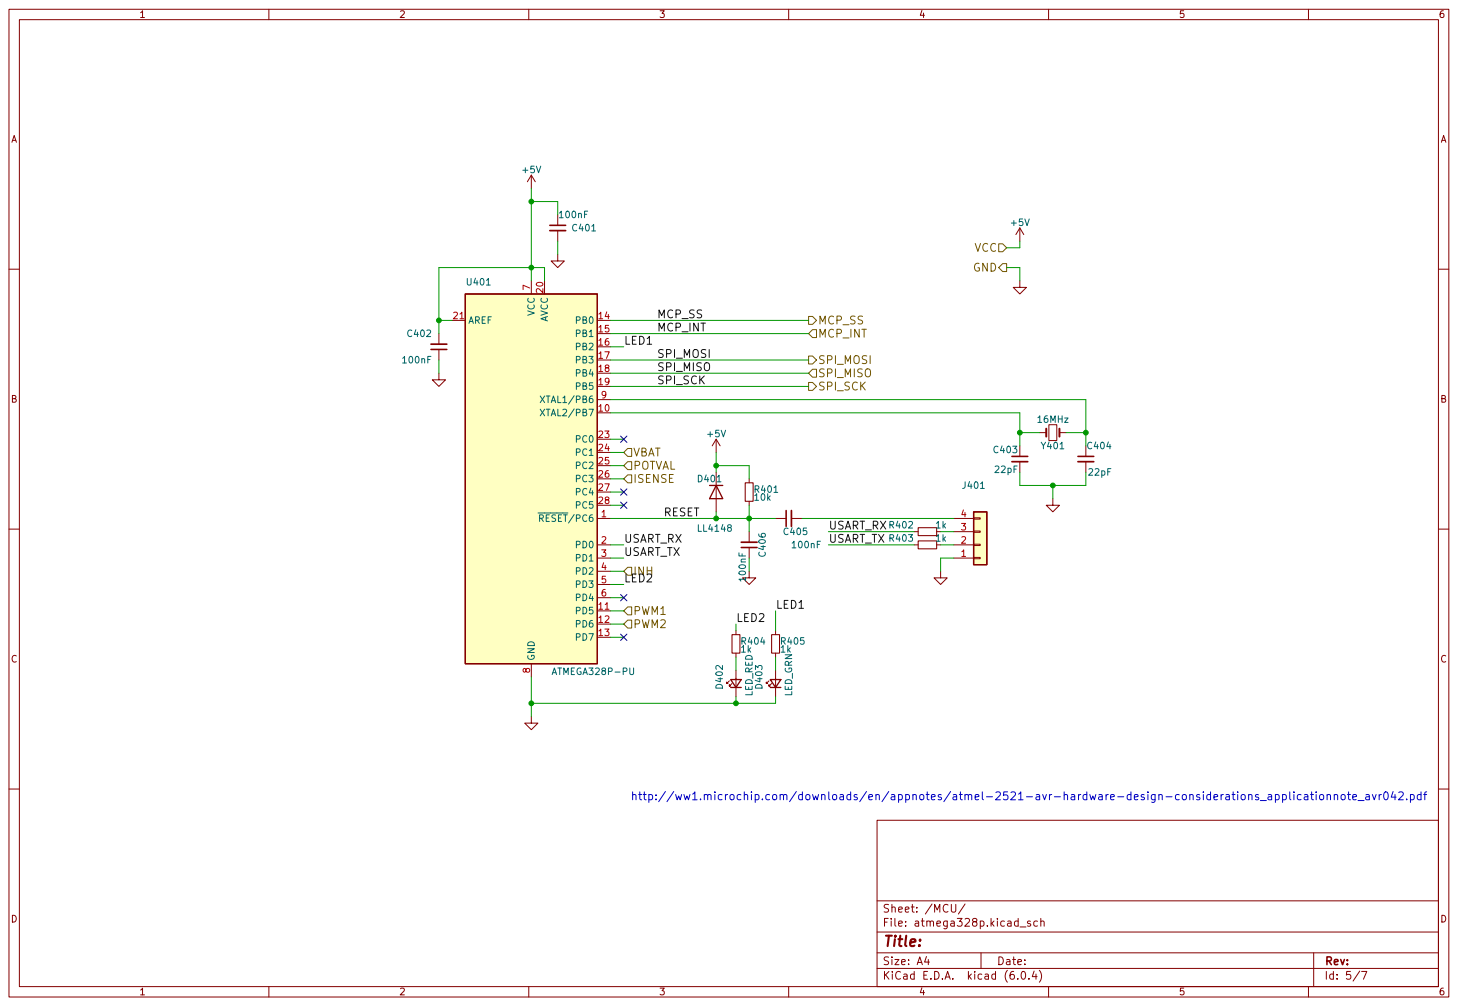
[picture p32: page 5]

http://ww1.microchip.com/downloads/en/appnotes/atmel-2521-avr-hardware-design-considerations_applicationnote_avr042.pdf

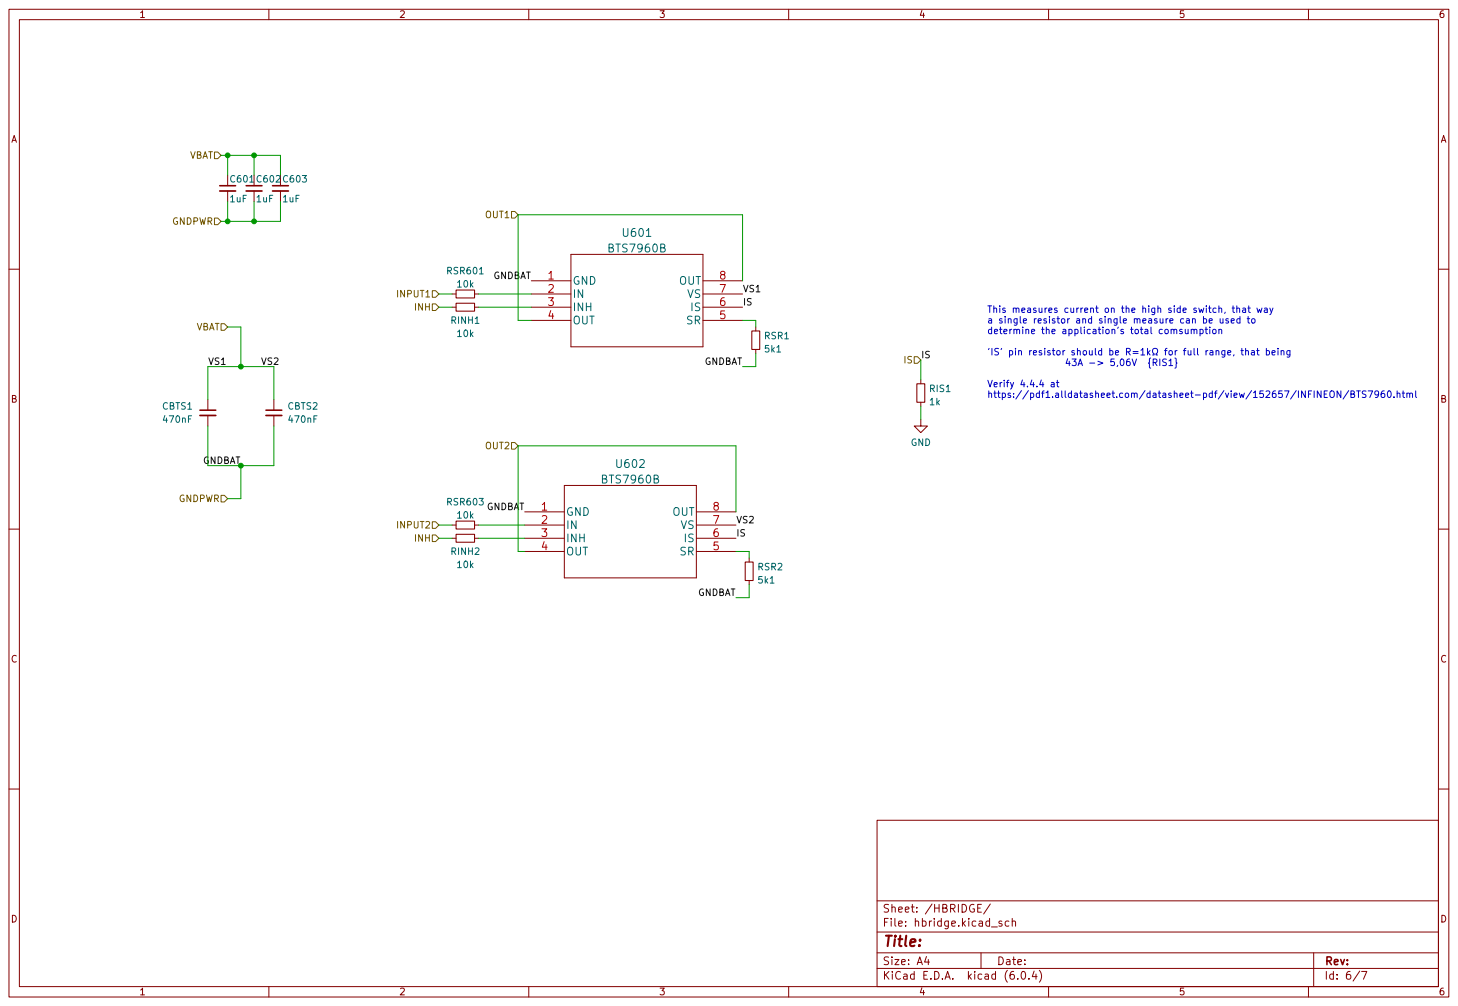
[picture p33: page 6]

This measures current on the high side switch, that way
a single resistor and single measure can be used to
determine the application's total comsumption

Verify 4.4.4 at
https://pdf1.alldatasheet.com/datasheet-pdf/view/152657/INFINEON/BTS7960.html

File: hbridge.kicad_sch Sheet: /HBRIDGE/ GND 1

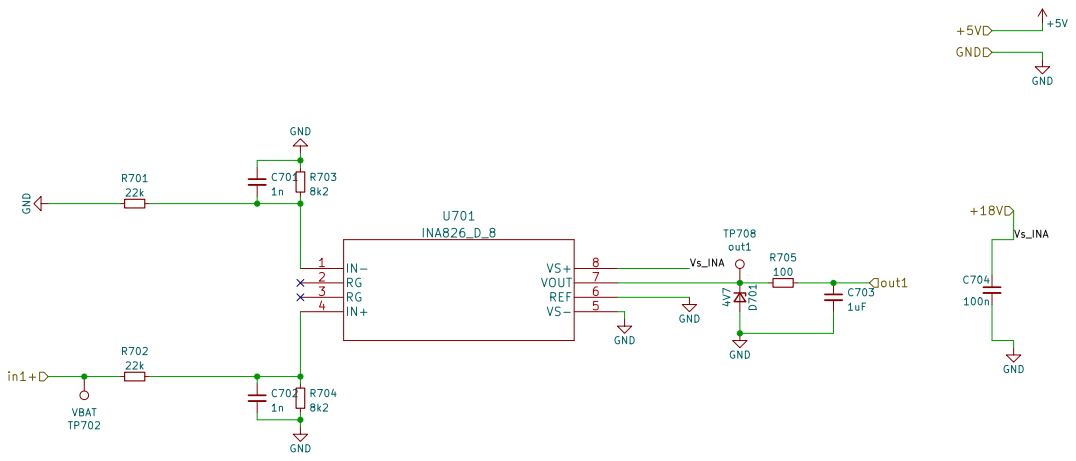
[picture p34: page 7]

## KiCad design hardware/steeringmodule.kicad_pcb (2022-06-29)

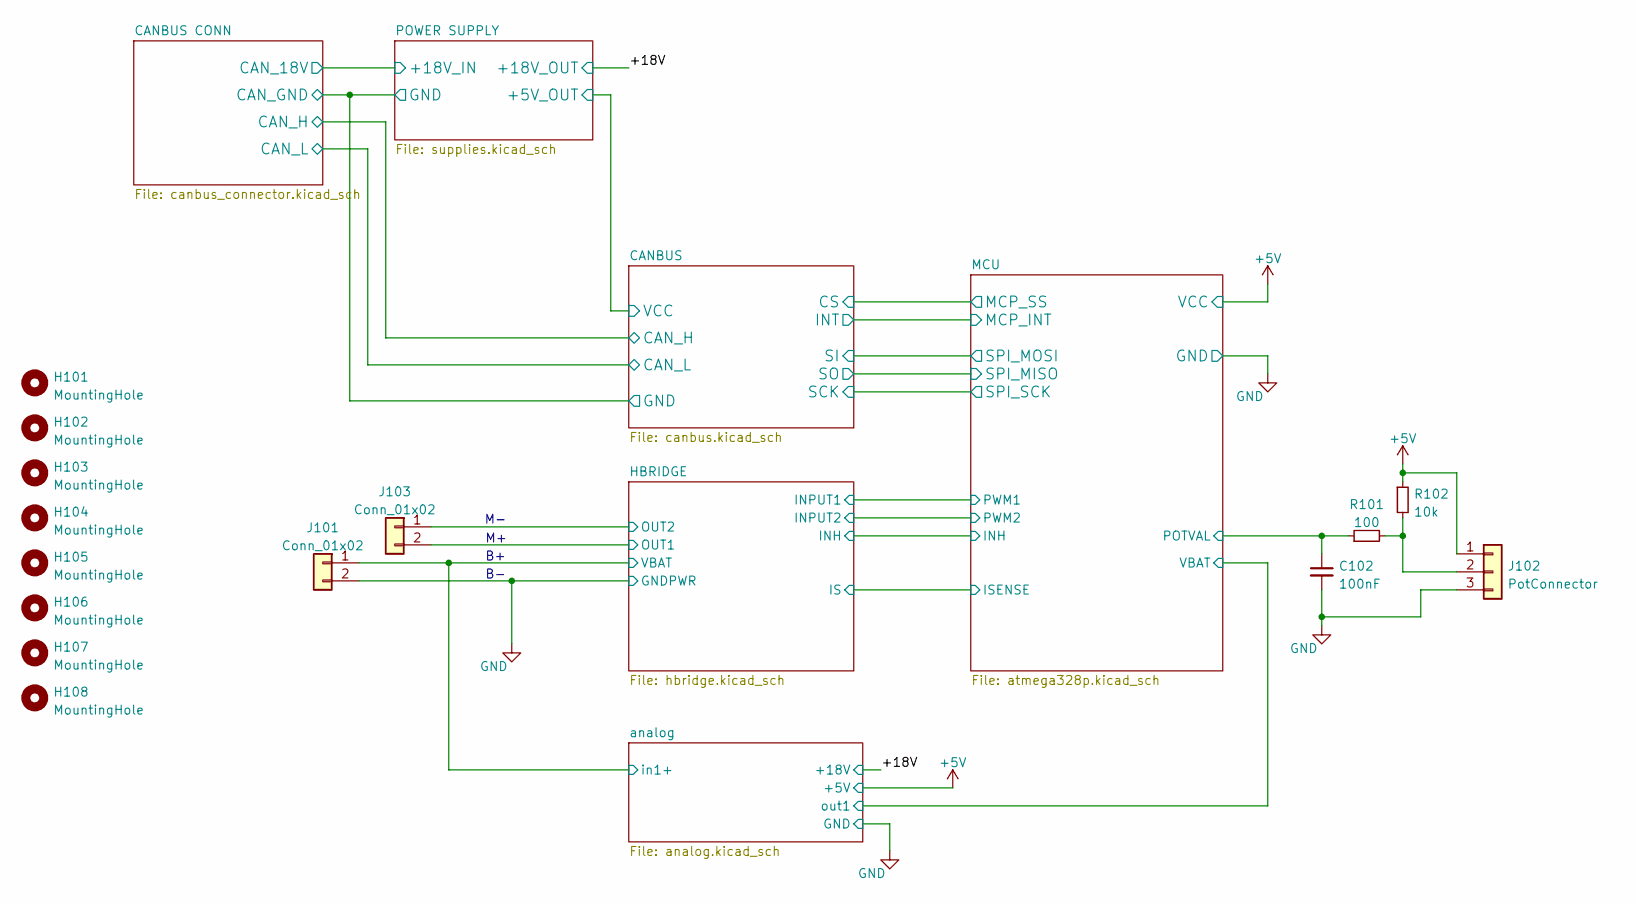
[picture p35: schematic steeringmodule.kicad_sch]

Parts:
C102: 100nF; C_0805_2012Metric_Pad1.18x1.45mm_HandSolder
H101, H102, H103, H104, H105, H106, H107, H108: MountingHole; MountingHole_3.2mm_M3
J101, J103: Conn_01x02; PhoenixContact_MSTBA_2,5_2-G-5,08_1x02_P5.08mm_Horizontal
J102: PotConnector; PhoenixContact_MSTBA_2,5_3-G-5,08_1x03_P5.08mm_Horizontal
R101: 100; R_0805_2012Metric_Pad1.20x1.40mm_HandSolder
R102: 10k; R_0805_2012Metric_Pad1.20x1.40mm_HandSolder

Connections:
/HBRIDGE/OUT1: J103.2; also elsewhere on the board
/HBRIDGE/OUT2: J103.1; also elsewhere on the board
/HBRIDGE/VS1: J101.1; also elsewhere on the board
/MCU/POTVAL: C102.1, R101.1; also elsewhere on the board
unnamed: J102.2, R101.2, R102.2

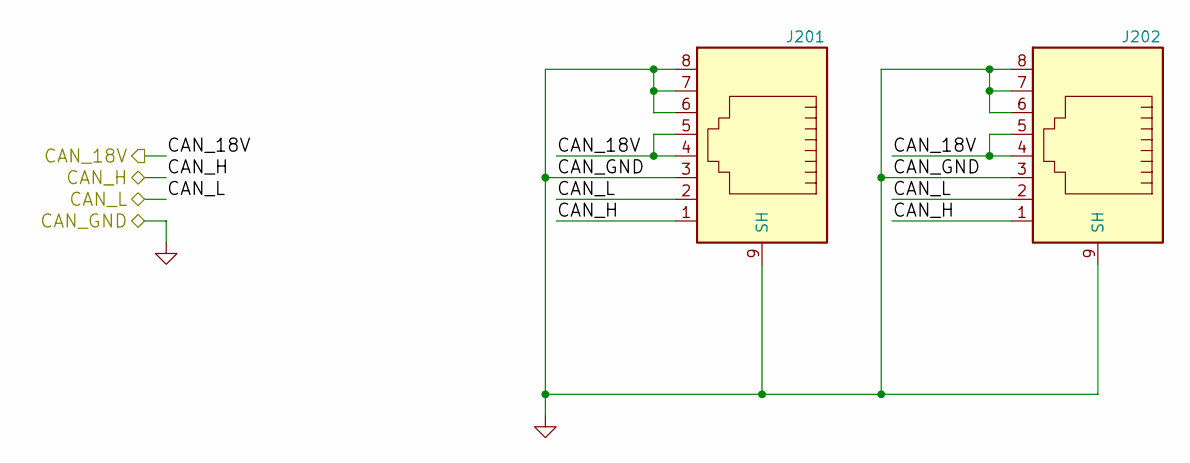
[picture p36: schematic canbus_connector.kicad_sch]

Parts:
J201, J202: RJ45_YH59_01

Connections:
/CANBUS CONN/CAN_18V: J201.4, J201.5, J202.4, J202.5; also elsewhere on the board
/CANBUS CONN/CAN_H: J201.1, J202.1; also elsewhere on the board
/CANBUS CONN/CAN_L: J201.2, J202.2; also elsewhere on the board

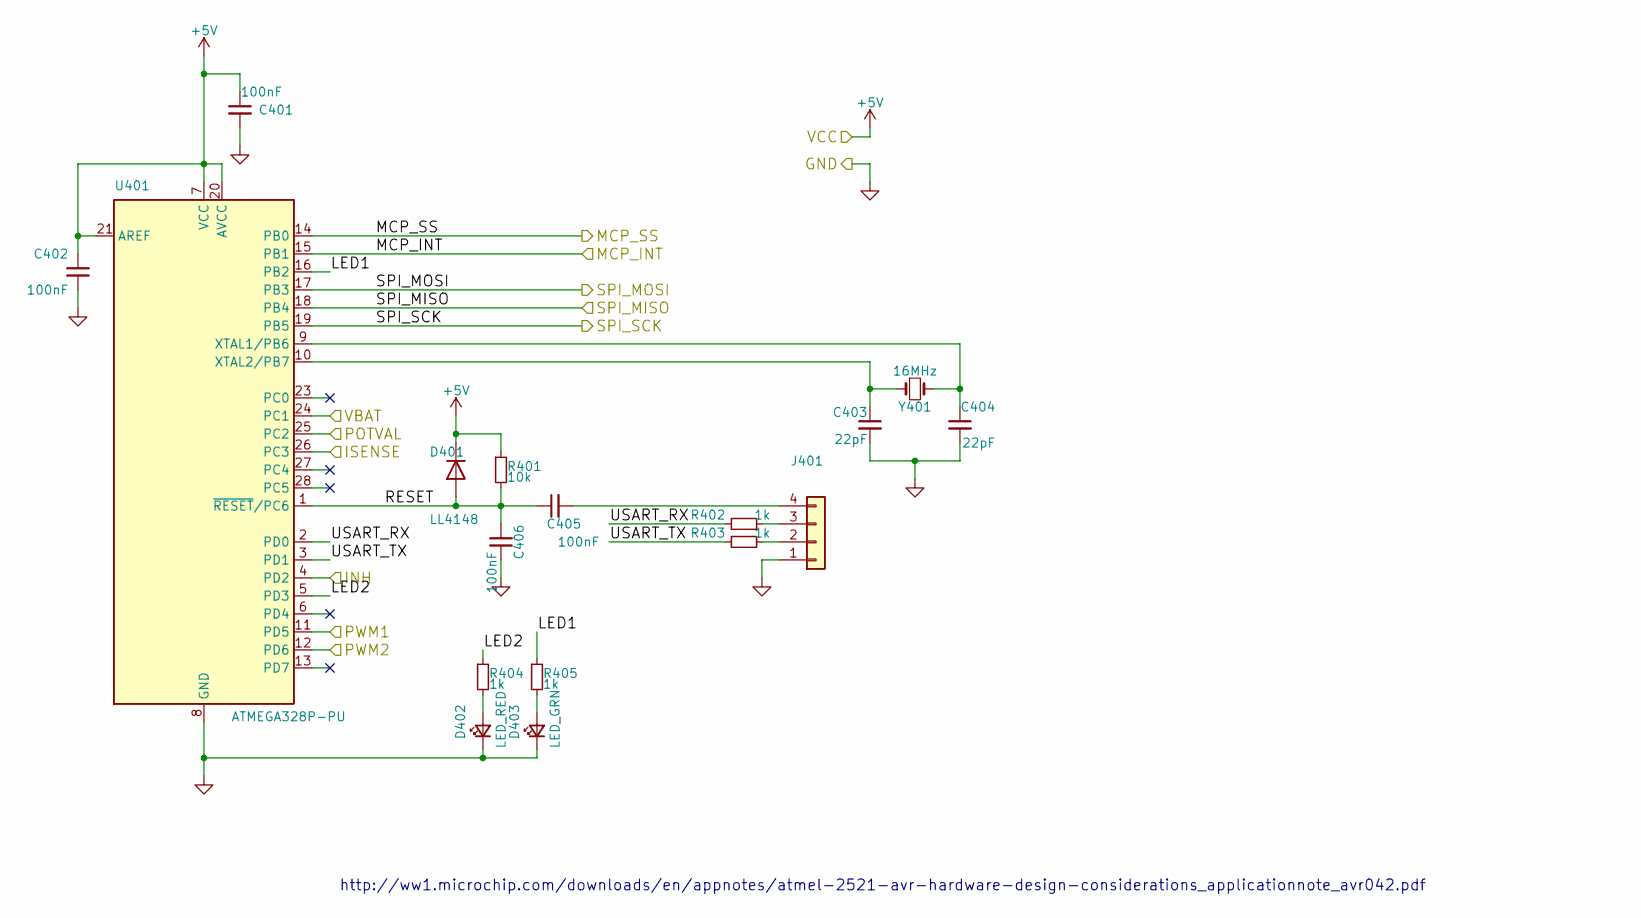
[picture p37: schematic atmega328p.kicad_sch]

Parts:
C401, C402, C405, C406: 100nF; C_0805_2012Metric_Pad1.18x1.45mm_HandSolder
C403, C404: 22pF; C_0805_2012Metric_Pad1.18x1.45mm_HandSolder
D401: LL4148; D_MiniMELF
D402: LED_RED; LED_0805_2012Metric_Pad1.15x1.40mm_HandSolder
D403: LED_GRN; LED_0805_2012Metric_Pad1.15x1.40mm_HandSolder
J401: PinHeader_1x04_P2.54mm_Vertical
R401: 10k; R_0805_2012Metric_Pad1.20x1.40mm_HandSolder
R402, R403, R404, R405: 1k; R_0805_2012Metric_Pad1.20x1.40mm_HandSolder
U401: ATMEGA328P-PU; DIP-28_W7.62mm_Socket
Y401: 16MHz; Crystal_HC49-U_Vertical

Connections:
/HBRIDGE/INH: U401.4 (PD2); also elsewhere on the board
/HBRIDGE/INPUT1: U401.11 (PD5); also elsewhere on the board
/HBRIDGE/INPUT2: U401.12 (PD6); also elsewhere on the board
/HBRIDGE/IS: U401.26 (PC3); also elsewhere on the board
/MCU/LED1: R405.1, U401.16 (PB2)
/MCU/LED2: R404.1, U401.5 (PD3)
/MCU/MCP_INT: U401.15 (PB1); also elsewhere on the board
/MCU/MCP_SS: U401.14 (PB0); also elsewhere on the board
/MCU/POTVAL: U401.25 (PC2); also elsewhere on the board
/MCU/RESET: C405.1, C406.2, D401.2 (A), R401.2, U401.1 (~RESET/PC6)
/MCU/SPI_MISO: U401.18 (PB4); also elsewhere on the board
/MCU/SPI_MOSI: U401.17 (PB3); also elsewhere on the board
/MCU/SPI_SCK: U401.19 (PB5); also elsewhere on the board
/MCU/USART_RX: R402.1, U401.2 (PD0)
/MCU/USART_TX: R403.1, U401.3 (PD1)
/MCU/VBAT: U401.24 (PC1); also elsewhere on the board
unnamed: C403.1, U401.10 (XTAL2/PB7), Y401.1
unnamed: C404.1, U401.9 (XTAL1/PB6), Y401.2
unnamed: C405.2, J401.4
unnamed: D402.2 (A), R404.2
unnamed: D403.2 (A), R405.2
unnamed: J401.2, R403.2
unnamed: J401.3, R402.2

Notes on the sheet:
http://ww1.microchip.com/downloads/en/appnotes/atmel-2521-avr-hardware-design-considerations_applicationnote_avr042.pdf

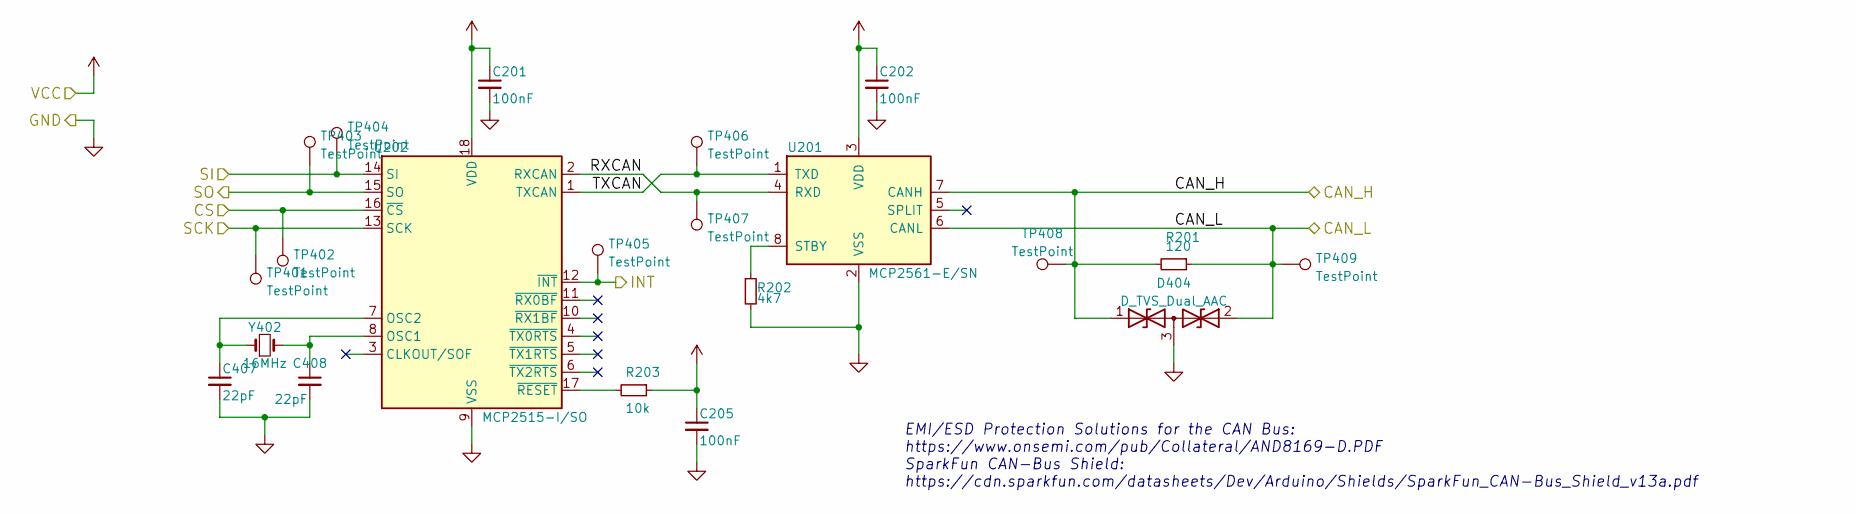
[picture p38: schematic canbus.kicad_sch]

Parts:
C201, C202, C205: 100nF; C_0805_2012Metric_Pad1.18x1.45mm_HandSolder
C407, C408: 22pF; C_0805_2012Metric_Pad1.18x1.45mm_HandSolder
D404: D_TVS_Dual_AAC; SOT-23
R201: 120; R_0805_2012Metric_Pad1.20x1.40mm_HandSolder
R202: 4k7; R_0805_2012Metric_Pad1.20x1.40mm_HandSolder
R203: 10k; R_0805_2012Metric_Pad1.20x1.40mm_HandSolder
TP401, TP402, TP403, TP404, TP405, TP406, TP407, TP408, TP409: TestPoint; TestPoint_Pad_2.0x2.0mm
U201: MCP2561-E/SN; SO-8_3.9x4.9mm_P1.27mm
U202: MCP2515-I/SO; SOIC-18W_7.5x11.6mm_P1.27mm
Y402: 16MHz; Crystal_HC49-U_Vertical

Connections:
/CANBUS CONN/CAN_H: D404.1 (A1), R201.2, TP408.1, U201.7 (CANH); also elsewhere on the board
/CANBUS CONN/CAN_L: D404.2 (A2), R201.1, TP409.1, U201.6 (CANL); also elsewhere on the board
/CANBUS/RXCAN: TP407.1, U201.4 (RXD), U202.2 (RXCAN)
/CANBUS/TXCAN: TP406.1, U201.1 (TXD), U202.1 (TXCAN)
/MCU/MCP_INT: TP405.1, U202.12 (~INT); also elsewhere on the board
/MCU/MCP_SS: TP402.1, U202.16 (~CS); also elsewhere on the board
/MCU/SPI_MISO: TP403.1, U202.15 (SO); also elsewhere on the board
/MCU/SPI_MOSI: TP404.1, U202.14 (SI); also elsewhere on the board
/MCU/SPI_SCK: TP401.1, U202.13 (SCK); also elsewhere on the board
unnamed: C407.1, U202.7 (OSC2), Y402.1
unnamed: C408.1, U202.8 (OSC1), Y402.2
unnamed: R202.1, U201.8 (STBY)
unnamed: R203.2, U202.17 (~RESET)

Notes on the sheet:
EMI/ESD Protection Solutions for the CAN Bus: https://www.onsemi.com/pub/Collateral/AND8169-D.PDF SparkFun CAN-Bus Shield: https://cdn.sparkfun.com/datasheets/Dev/Arduino/Shields/SparkFun_CAN-Bus_Shield_v13a.pdf

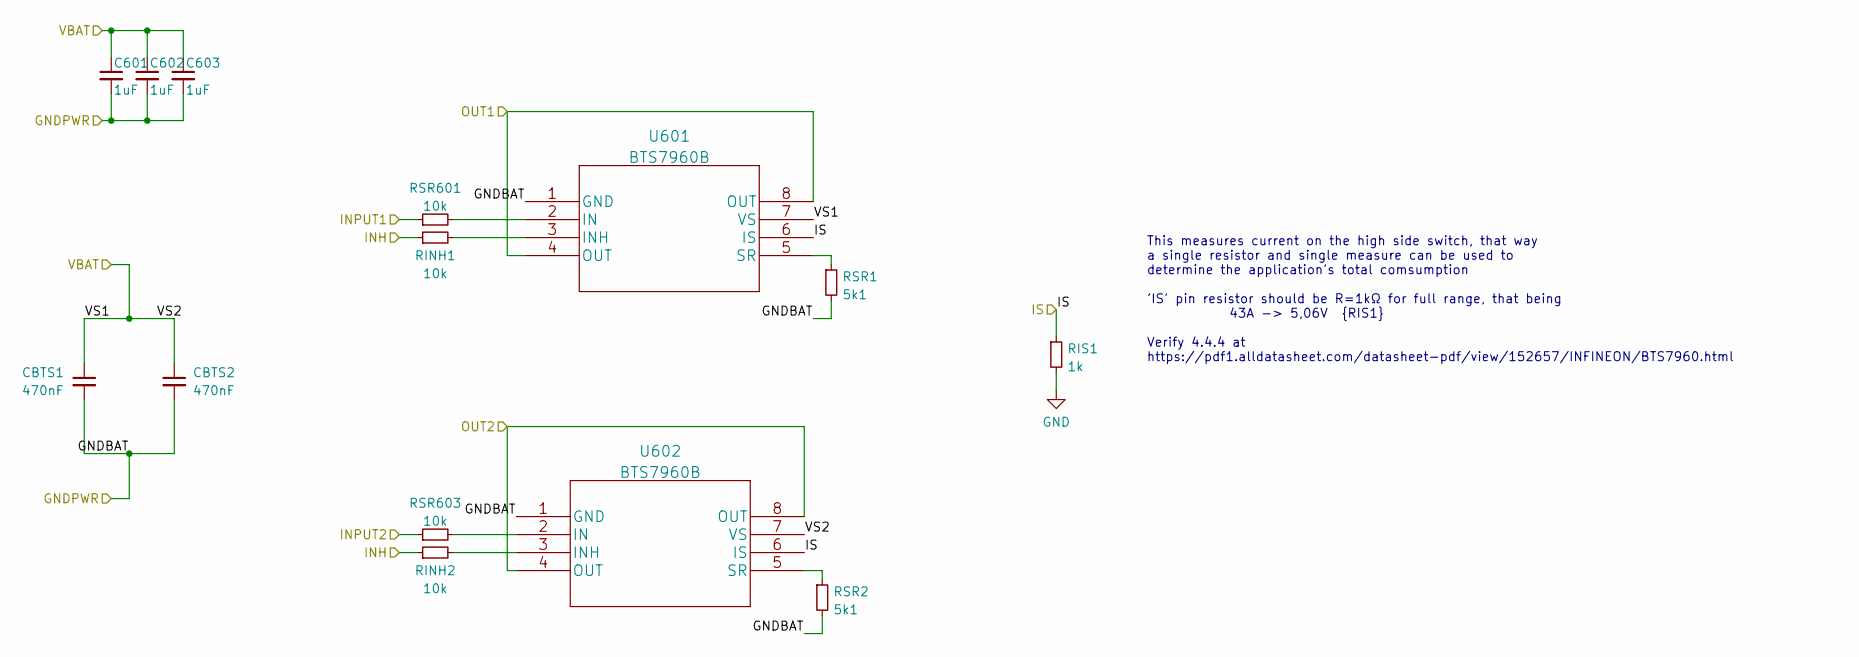
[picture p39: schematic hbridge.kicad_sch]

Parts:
C601, C602, C603: 1uF; C_1206_3216Metric_Pad1.33x1.80mm_HandSolder
CBTS1, CBTS2: 470nF; C_0805_2012Metric_Pad1.18x1.45mm_HandSolder
RINH1, RINH2: 10k; R_0805_2012Metric_Pad1.20x1.40mm_HandSolder
RIS1: 1k; R_0805_2012Metric_Pad1.20x1.40mm_HandSolder
RSR1, RSR2: 5k1; R_0805_2012Metric_Pad1.20x1.40mm_HandSolder
RSR601, RSR603: 10k; R_0805_2012Metric_Pad1.20x1.40mm_HandSolder
U601, U602: BTS7960B; TO-263-7_TabPin8

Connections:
/HBRIDGE/INH: RINH1.1, RINH2.1; also elsewhere on the board
/HBRIDGE/INPUT1: RSR601.1; also elsewhere on the board
/HBRIDGE/INPUT2: RSR603.1; also elsewhere on the board
/HBRIDGE/IS: RIS1.1, U601.6 (IS), U602.6 (IS); also elsewhere on the board
/HBRIDGE/OUT1: U601.4 (OUT), U601.8 (OUT); also elsewhere on the board
/HBRIDGE/OUT2: U602.4 (OUT), U602.8 (OUT); also elsewhere on the board
/HBRIDGE/VS1: C601.1, C602.1, C603.1, CBTS1.1, CBTS2.1, U601.7 (VS), U602.7 (VS); also elsewhere on the board
unnamed: RINH1.2, U601.3 (INH)
unnamed: RINH2.2, U602.3 (INH)
unnamed: RSR1.1, U601.5 (SR)
unnamed: RSR2.1, U602.5 (SR)
unnamed: RSR601.2, U601.2 (IN)
unnamed: RSR603.2, U602.2 (IN)

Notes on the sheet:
This measures current on the high side switch, that way a single resistor and single measure can be used to determine the application's total comsumption 'IS' pin resistor should be R=1kΩ for full range, that being 43A -> 5,06V {RIS1} Verify 4.4.4 at https://pdf1.alldatasheet.com/datasheet-pdf/view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

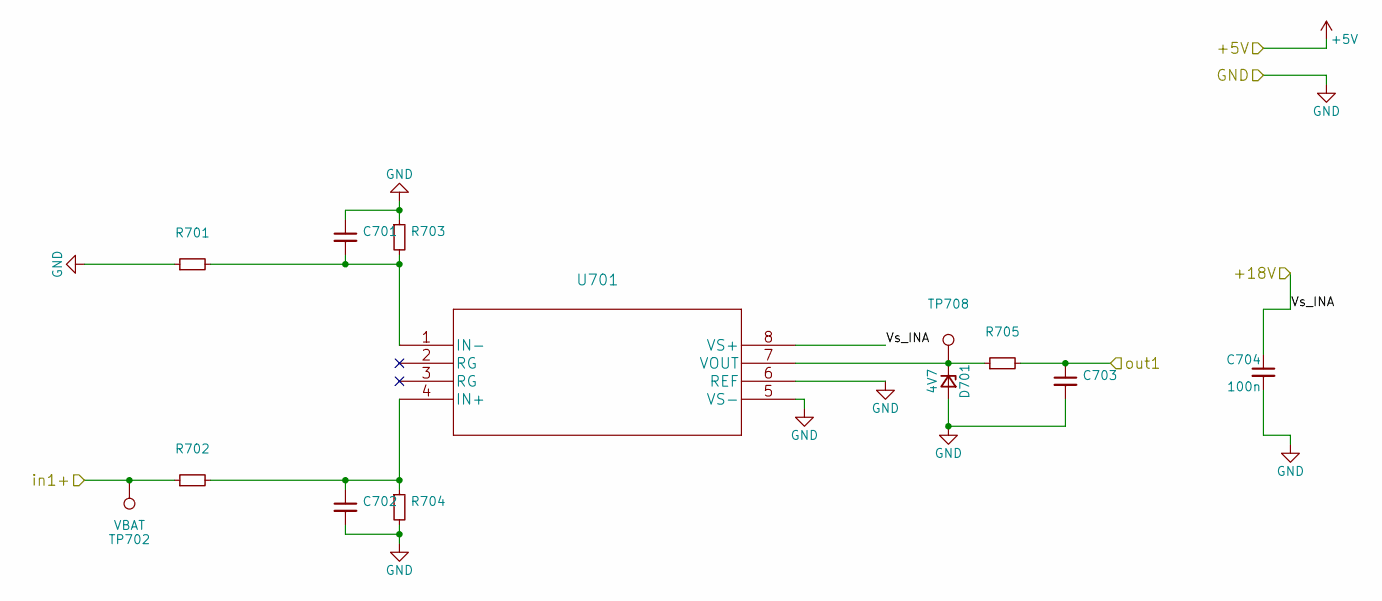
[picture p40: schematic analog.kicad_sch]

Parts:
C701, C702, C703: (no value)
C704: 100n; C_0805_2012Metric_Pad1.18x1.45mm_HandSolder
D701: 4V7; D_MiniMELF_Handsoldering
R701, R702, R703, R704, R705: (no value)
TP702: VBAT; TestPoint_Pad_2.0x2.0mm
TP708: (no value)
U701: (no value)

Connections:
/+18V: C704.1, U701.8 (VS+); also elsewhere on the board
/HBRIDGE/VS1: R702.1, TP702.1; also elsewhere on the board
/MCU/VBAT: C703.1, R705.2; also elsewhere on the board
unnamed: C701.2, R701.2, R703.2, U701.1 (IN-)
unnamed: C702.1, R702.2, R704.1, U701.4 (IN+)
unnamed: D701.1 (K), R705.1, TP708.1, U701.7 (VOUT)

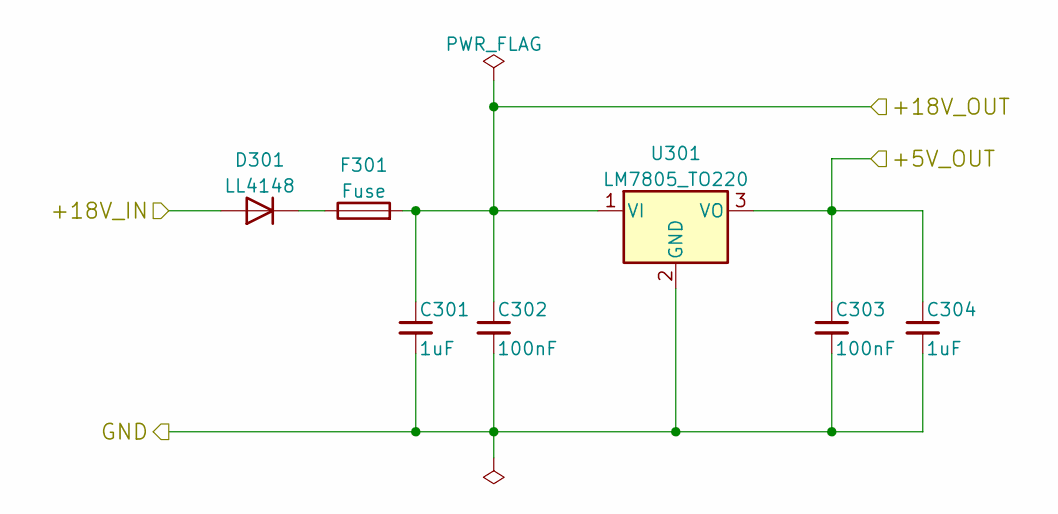
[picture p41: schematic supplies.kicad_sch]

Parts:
C301, C304: 1uF; C_1206_3216Metric_Pad1.33x1.80mm_HandSolder
C302, C303: 100nF; C_0805_2012Metric_Pad1.18x1.45mm_HandSolder
D301: LL4148; D_MiniMELF
F301: Fuse; Fuse_1206_3216Metric_Pad1.42x1.75mm_HandSolder
U301: LM7805_TO220; TO-220-3_Horizontal_TabDown_SMD

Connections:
/+18V: C301.1, C302.1, F301.2, U301.1 (VI); also elsewhere on the board
/CANBUS CONN/CAN_18V: D301.2 (A); also elsewhere on the board
unnamed: D301.1 (K), F301.1

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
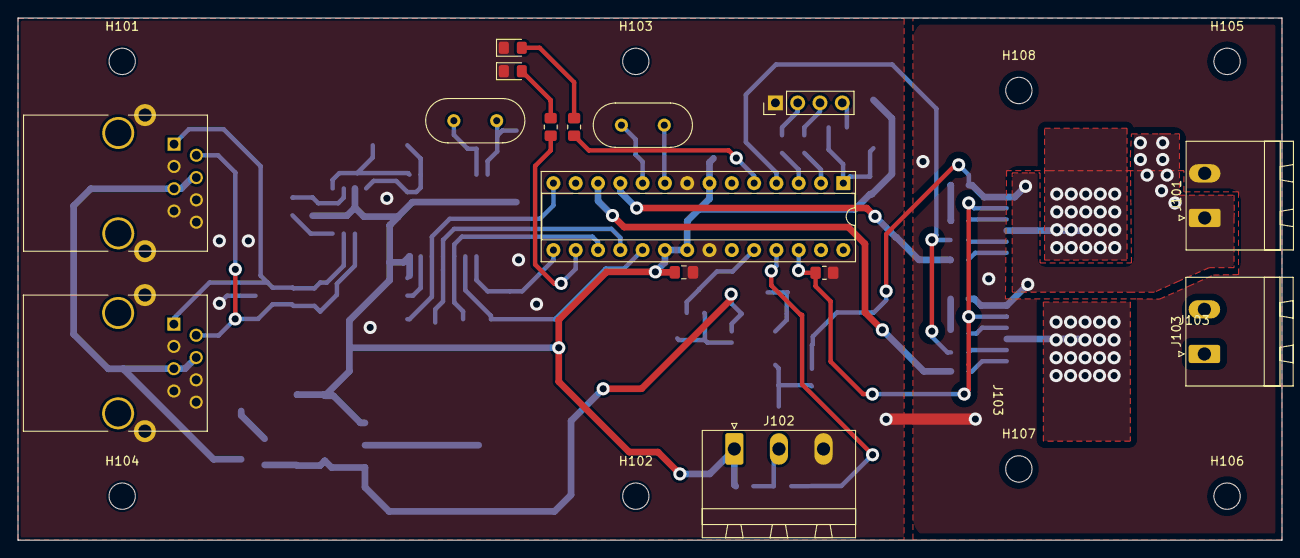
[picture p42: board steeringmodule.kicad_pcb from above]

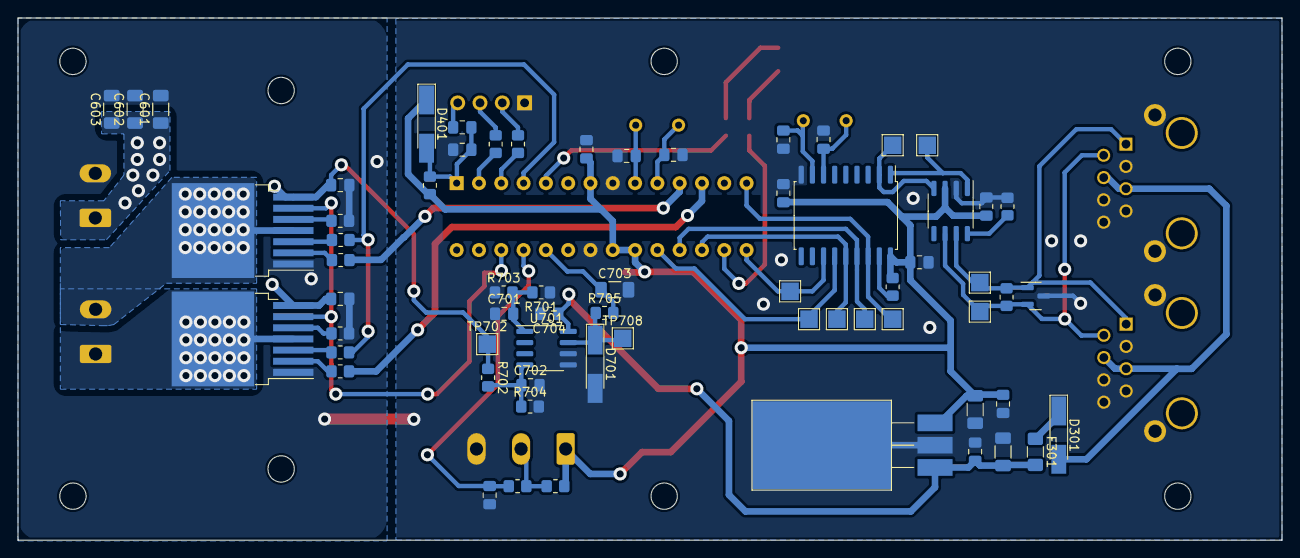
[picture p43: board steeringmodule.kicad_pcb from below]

Board: 2 copper layers, 144.0 x 59.5 mm, 88 parts (65 on the bottom side), 49 nets.

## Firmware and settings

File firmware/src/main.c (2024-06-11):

// coding: utf-8

#include "main.h"

void init(void)
{

    #ifdef USART_ON
        usart_init(MYUBRR,1,1);                         // inicializa a usart
        VERBOSE_MSG_INIT(usart_send_string("\n\n\nUSART.. OK!\n"));
    #endif

    _delay_ms(200);

    #ifdef WATCHDOG_ON
        VERBOSE_MSG_INIT(usart_send_string("WATCHDOG..."));
        wdt_init();
        VERBOSE_MSG_INIT(usart_send_string(" OK!\n"));
        wdt_reset();
    #else
        VERBOSE_MSG_INIT(usart_send_string("WATCHDOG... OFF!\n"));
    #endif

    #ifdef WATCHDOG_ON
        wdt_reset();
    #endif

    #ifdef SPI_ON
        set_bit(DDRB, PB2);     //output to be the spi master
        
    #endif

    #ifdef CAN_ON
        VERBOSE_MSG_INIT(usart_send_string("CAN (500kbps)..."));
        #ifdef LED_ON
            set_bit(LED2_PORT, LED2);
        #endif  
        can_init(BITRATE_500_KBPS);
        //can_set_mode(LOOPBACK_MODE);
        VERBOSE_MSG_INIT(usart_send_string(" OK!\n"));
        VERBOSE_MSG_INIT(usart_send_string("CAN filters..."));
        can_static_filter(can_filter);
        VERBOSE_MSG_INIT(usart_send_string(" OK!\n"));
    #else
        VERBOSE_MSG_INIT(usart_send_string("CAN... OFF!\n"));
        clr_bit(LED2_PORT, LED2);
    #endif

    #ifdef WATCHDOG_ON
        wdt_reset();
    #endif

    #ifdef ADC_ON
        VERBOSE_MSG_INIT(usart_send_string("ADC..."));
        adc_init();
        VERBOSE_MSG_INIT(usart_send_string(" OK!\n"));
    #else
        VERBOSE_MSG_INIT(usart_send_string("ADC... OFF!\n"));
    #endif

    #ifdef WATCHDOG_ON
        wdt_reset();
    #endif

    #ifdef SLEEP_ON 
        VERBOSE_MSG_INIT(usart_send_string("SLEEP..."));
        sleep_init();
        VERBOSE_MSG_INIT(usart_send_string(" OK!\n"));
    #else
        VERBOSE_MSG_INIT(usart_send_string("SLEEP... OFF!\n"));
    #endif

    #ifdef WATCHDOG_ON
        wdt_reset();
    #endif

 	#ifdef MACHINE_ON
        VERBOSE_MSG_INIT(usart_send_string("MACHINE..."));
		machine_init();
        VERBOSE_MSG_INIT(usart_send_string(" OK!\n"));
    #else
        VERBOSE_MSG_INIT(usart_send_string("MACHINE... OFF!\n"));
	#endif

    #ifdef WATCHDOG_ON
        wdt_reset();
    #endif
	
    #ifdef HBRIDGE_ON
        VERBOSE_MSG_INIT(usart_send_string("HBRIDGE..."));
        hbridge_init();
        VERBOSE_MSG_INIT(usart_send_string(" OK!\n"));
    #else
        VERBOSE_MSG_INIT(usart_send_string("MACHINE... OFF!\n"));
    #endif

    #ifdef WATCHDOG_ON
        wdt_reset();
    #endif
    
    #ifdef LED_ON
        set_bit(DDRD, LED1);                      // LED como saída
        set_bit(DDRB, LED2);                      // LED como saída
        VERBOSE_MSG_INIT(usart_send_string("LED... OK!\n"));
    #else
        VERBOSE_MSG_INIT(usart_send_string("LED... OFF!\n"));
    #endif

    #ifdef WATCHDOG_ON
        wdt_reset();
    #endif

    #ifdef MACHINE_ON
        print_configurations();
    #endif // MACHINE_ON

    sei();
}

int main(void)
{
    init();
   
	for(;;){
		#ifdef WATCHDOG_ON
            wdt_reset();
		#endif

        #ifdef MACHINE_ON
            machine_run();
        #endif

		#ifdef SLEEP_ON
            //sleep_mode();
		#endif

	}
}


/**
 * @brief se em debug, fica chaveando os pinos de debugs até o reset do watchdog
 */
ISR(BADISR_vect)
{
    for(;;){
        VERBOSE_MSG_ERROR(usart_send_string("\nFATAL ERROR: BAD ISR."));
        #ifdef WATCHDOG_ON
            VERBOSE_MSG_ERROR(usart_send_string("WAITING FOR WATCHDOG TO RESET...\n"));
        #endif
        #ifdef DEBUG_ON
            DEBUG0;
            DEBUG1;
            _delay_ms(100);
        #endif
    }
}

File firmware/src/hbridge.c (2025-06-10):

#include "hbridge.h"
#include "math.h"
volatile float duty_coeff;
volatile int tail_diff;
volatile int tail_diff_old;
volatile int duty_msg;
volatile uint32_t hbridge_verbose_clk_div;
volatile uint8_t hbridge_led_clk_div;
volatile uint8_t hbridge_led_clk_var;
volatile hbridge_flags_t hbridge_flags;

float PI(float r, float y);

void hbridge_init(void)
{   
    TCCR0A = (1<<COM0A1) | (1<<COM0A0)              // Set on compare match when up-counting, clear ... on down-counting
            | (1<<COM0B1)| (0<<COM0B0)              // Clear on compare match when up-counting, set ... on down-counting
            | (0<< WGM01) | (1<<WGM00);              

    // fOCnxPCPWM = (fclk_IO)/(N x 510), N being the prescaler
    // Prescaler 010 = 8 -> 3921.5 Hz               // Used IC operates up to 25kHz, this timer presents minimum prescaler of either 1 or 8 
    TCCR0B = (0<<WGM02) | (0<<CS02) | (1<<CS01) | (0<<CS00);                           

    // Sets the OC0A and OC0B duty cycle, remenber Timer/Counter0 is 8bits
    TCNT0 = 0;
    OCR0A = 255;       // No PWM 
    OCR0B = 0;         // No PWM


// Set pins as output DDRxn = 1
    set_bit(HBRIDGE_PWM_DDR, HBRIDGE_PWM_PIN1);
    set_bit(HBRIDGE_PWM_DDR, HBRIDGE_PWM_PIN2);
    set_bit(HBRIDGE_PWM_DDR, HBRIDGE_ENABLE_PIN);
    
// Initiate HBRIDGE disabled;
    clr_bit(HBRIDGE_PORT, HBRIDGE_ENABLE_PIN);

    tail_diff = 0;
    tail_diff_old = 0;
    duty_coeff = 0;
    
    hbridge_flags.all__ = 0;
    hbridge_flags.force_center = 1;
}

/**
 * @brief Sets pwm duty cycle value on OCR identified by 'side'
 * 
 * @param side : Identify switching side (OCR0A or OCR0B)
 * @param duty : duty cycle
 * @return uint8_t 
 */
uint8_t hbridge_set_pwm(uint8_t side, float duty)
{
    if(duty < 0){
        duty = 0;
    }
    if (side == HBRIDGE_SIDE_A){
        OCR0A = (int)(0xff * (1 - duty));
        return HBRIDGE_OK;
    }else if (side == HBRIDGE_SIDE_B){
        OCR0B = (int)(0xff * duty);
        return HBRIDGE_OK;
    }else{
        return HBRIDGE_ERROR;
    }
}

/**
 * @brief 
 * 
 */
void hbridge_task(void)
{
    
    // Check for errors 
    if (measurements.position_avg > 254){
        //error_flags.invalid_tail = 1;
        //set_state_error();
    }

    // Safeguard for no_mic and steering wheel angle
    // If mic responds and str_whl_angle < 270, hbridge if fine
    if(can_app_flags.no_mic == 1) {
        hbridge_flags.force_center = 1;
    } else {
        if(str_whl_position > 254) {
            //hbridge_flags.force_center = 1;
            //usart_send_string("Invalid str wheel angle, value > 270.\n");
        } else {
            hbridge_flags.force_center = 0;
        }
    }

    // Enable for operation
    if(!tst_bit(HBRIDGE_PORT, HBRIDGE_ENABLE_PIN)) {
        set_bit(HBRIDGE_PORT, HBRIDGE_ENABLE_PIN);
        usart_send_string("HBridge is enabled!\n");
    }

// Operation
    if(hbridge_flags.force_center == 1){
        str_whl_position = 158;
    }


#ifdef VERBOSE_ON_HBRIDGE
    if(hbridge_verbose_clk_div++ >= HBRIDGE_VERBOSE_CLK_DIV){

        if (tail_diff > TAIL_TOLERANCE){
            VERBOSE_MSG_HBRIDGE(usart_send_string("BORESTE \t\t"));
        } else if (tail_diff < -TAIL_TOLERANCE) { 
            VERBOSE_MSG_HBRIDGE(usart_send_string("BOMBORDO\t\t"));
        } else {
            VERBOSE_MSG_HBRIDGE(usart_send_string("Parado  \t\t"));
        }
        VERBOSE_MSG_HBRIDGE(usart_send_string("Side Switching: "));
        VERBOSE_MSG_HBRIDGE(usart_send_uint8(hbridge_flags.all__));usart_send_string

        VERBOSE_MSG_HBRIDGE(usart_send_string("\tDuty coeff: "));
        VERBOSE_MSG_HBRIDGE(usart_send_int16(duty_msg));
        
        VERBOSE_MSG_HBRIDGE(usart_send_string("\t Taildiff Old: "));
        VERBOSE_MSG_HBRIDGE(usart_send_int16(tail_diff_old));

        if (hbridge_flags.force_center == 1) {
        VERBOSE_MSG_HBRIDGE(usart_send_char('\t'));
        VERBOSE_MSG_HBRIDGE(usart_send_string("Tail shall be centered.\n"));
        }
        VERBOSE_MSG_HBRIDGE(usart_send_char('\n'));
        hbridge_verbose_clk_div = 0;
    }
#endif

#ifdef LED_ON
    // Led 1 displays whether force_center is set (slow means that it's set)    
    if (hbridge_flags.force_center == 1){
        hbridge_led_clk_var = 90;
    } else {
        hbridge_led_clk_var = 15;
    }
    
    if (hbridge_led_clk_div++ >= hbridge_led_clk_var){
        cpl_bit(LED1_PORT, LED1);
        hbridge_led_clk_div = 0;
    }
#endif

}

//TODO: Calculate constants
#define PERIOD 0.0019439999999999998

#define D_MAX 93

float PI(float r, float y){
    // PI CONFIGURATIONS:
    const float Kp = 2.5;         // analog series proportional gain

    // Compute error:
    float e1 = r -y;
	float u;

    // Compute control action:
    u = Kp * e1;

    // Anti windup
    if(u < -D_MAX)           u = -D_MAX;
    else if(u > D_MAX)      u = D_MAX;

    return u;
}

#define STR_MAX_ANGLE 900.0f
#define STR_MIN_ANGLE -900.0f
#define D_MIN 0.25f

void hbridge_control(float angle)
{
    float dt;
    float position_setpoint = str_whl_position - 135.0f;
    angle -= 135.0f;

    if (position_setpoint > STR_MAX_ANGLE) position_setpoint = STR_MAX_ANGLE;
    if (position_setpoint < STR_MIN_ANGLE) position_setpoint = STR_MIN_ANGLE;

    dt = PI(position_setpoint, angle);
    dt = dt/100.0f;
    static uint16_t send_clk;

    if (++send_clk >= 50){
        send_clk = 0;

        // usart_send_float(position_setpoint);
        // usart_send_string(",");
        // usart_send_float(angle);
        // usart_send_string(",");
        // usart_send_float(dt*99);
        // usart_send_char(',');
        // usart_send_float(batvoltage);
        // usart_send_char(',');
        // usart_send_float(batcurrent);
        // usart_send_char('\n');
    }

    if (fabs(dt) < D_MIN)
        dt = 0.0f;

    if (dt < 0){
        hbridge_set_pwm(HBRIDGE_SIDE_A, -dt);
        hbridge_set_pwm(HBRIDGE_SIDE_B, 0);   
    } else{
        hbridge_set_pwm(HBRIDGE_SIDE_A, 0);
        hbridge_set_pwm(HBRIDGE_SIDE_B, dt);
    }
}

EMPTY_INTERRUPT(TIMER0_COMPA_vect);
EMPTY_INTERRUPT(TIMER0_COMPB_vect);
EMPTY_INTERRUPT(TIMER0_OVF_vect);

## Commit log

2022-06-08 hardware: Protótipo da PCB
    [atmega328p.kicad_sch, canbus.kicad_sch, canbus_connector.kicad_sch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]
2022-06-15 hardware: added 3D IMG archives and schematic PDF
    [steeringmodule.kicad_pcb, steeringmodule.kicad_sch]
2022-06-21 Added analog stage for Vbat measurement, and it's simulation
    [analog.kicad_sch, atmega328p.kicad_sch, canbus_connector.kicad_sch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]
2022-06-21 Adjusted analog, now using INA826. Simulations updated.
    [analog.kicad_sch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]
2022-06-29 hardware: added shapes 3D
    [K78Lxx-1000R3.stp, steeringmodule.kicad_pcb]
2022-07-15 Changed ADC timer0->timer1, added can msg measurements
2022-07-16 gitignore, fixed adc variables declaration errors
    [adc.c, conf.h]
2022-07-18 Leds use different ports, defined now
2022-07-18 No longer using '_led' functions because of different ports
    [main.c]
2022-07-18 Board on running state
2022-07-19 Redefined registers for Timer/Counter1 Compare Match B
2022-07-19 Set SS pin
2022-07-19 ADC Compares with OCIE1B, changed emprt int to timer1_compB
2022-07-19 Deleted aditional ADC frequency definitions
2022-07-19 Change to registers, ISR still not working
    [adc.c]
2022-07-19 Deleted VERBOSE for additional ADC config
2022-07-19 Fixed prescaler on 64 to test clock selection
    [adc.c]
2022-07-19 ADC working properly. Usart messages removed.
2022-07-19 No fake adc
2022-07-19 Removed unused ADC variables. task_running contains usart msgs for adc troubleshooting.
2022-07-20 adc variables are type float, vcoeff correct
    [adc.c]
2022-07-20 CAN ON, adc working properly (pot not linear)
2022-07-20 Messages ON, led clk div altered for demo
2022-07-21 Dummy forgot to change CAN_SIGNATURE_SELF, corrected
    [conf.h]
2022-07-21 ADC and CAN working
2022-07-23 Add hbridge set pwm and related variables
2022-07-23 Working pwm, hbridge_set_pwm added
2022-07-25 Tail and steering wheel position is limited as 270
2022-07-26 Testing deleted, added tst_bit on enable bridge and error flag if angle>270
    [hbridge.c]
2022-07-26 Added tail tolerance and side_switch_clk_div (prototype)
    [conf.h]
2022-07-26 No longer takes measurements in running nor flips led
2022-07-26 hbridge_flags, duty_coeff, and side_switch prototype
2022-07-26 Init on flag force_center, wrong side check, verbose msgs
    [hbridge.c]
2022-07-27 Reset dail diff if 0
    [hbridge.c]
2022-07-28 Imagens para o README
2022-07-29 Correctec comment that was being executed
    [hbridge.c]
2022-07-29 Created BOM, removed Testpoints from it.
    [analog.kicad_sch, canbus.kicad_sch, steeringmodule.csv]
2022-07-29 Correção de texto, hyperlink e imagens
2022-07-29 Resize PCB image
2022-07-29 Renomeando o vídeo de funcionamento
2022-08-16 Documentation, organized hbridge_task error checks
    [hbridge.c]
2022-09-08 Changed led_clk_div
2022-09-08 Organized 'if' statements in bridge operation, corrected documentation
    [hbridge.c]
2022-09-25 Reduced led_clk_div 50 -> 10
2022-09-26 LED2 OFF if CAN OFF
2022-09-26 Corrected assignment of duty_coeff value, led1 blink freq changes according to force_center
    [hbridge.c]
2022-10-02 Change coefficients to max angle 256, decrease led blink frequency if no_mic
2022-10-02 ToDo: Fix batcurrent coefficient
    [adc.c]
2022-11-11 LED2 with can_app_send_measurements frequency
2022-11-11 Changed idle and initializing led1 to led2
2023-10-19 generate bom
2024-06-11 fix: fix atmega freezing when sending float via UART
    [conf.h, hbridge.c, main.c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]
2025-06-10 define print infos
2025-06-10 better print infos
2025-10-15 standard should be defined PRINT_INFOS
